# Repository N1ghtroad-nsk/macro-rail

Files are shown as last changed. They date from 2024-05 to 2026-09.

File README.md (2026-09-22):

# Macro Slider | Слайдер для макросъемки

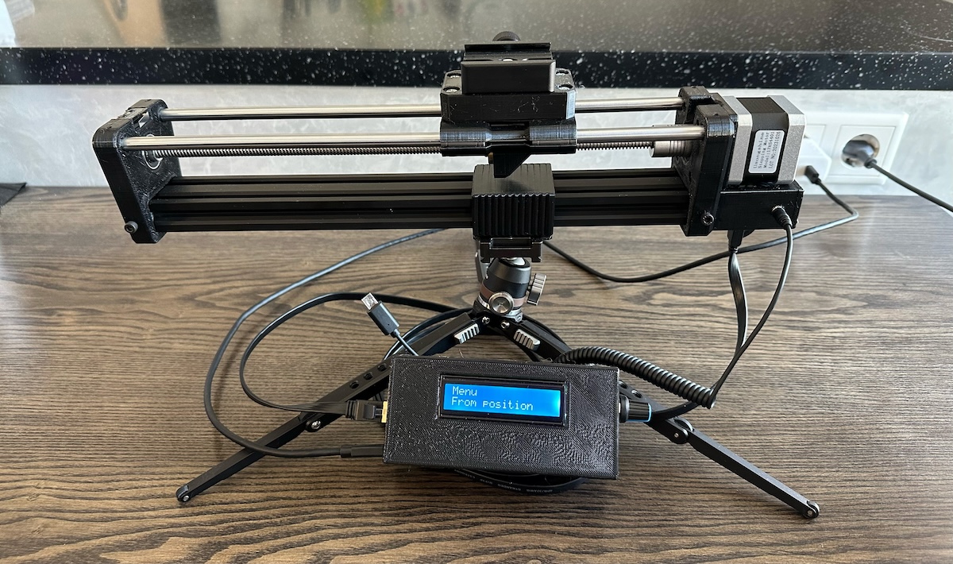
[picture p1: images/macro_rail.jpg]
Macro Rail


- [Macro Slider | Слайдер для макросъемки](#macro-slider--слайдер-для-макросъемки)
- [RU](#ru)
  - [Структура](#структура)
  - [Компоненты](#компоненты)
    - [Пульт](#пульт)
    - [Рельса](#рельса)
    - [Крепление](#крепление)
  - [Схема](#схема)
  - [Arduino](#arduino)
    - [Зависимости](#зависимости)
    - [Настройка](#настройка)
- [EN](#en)
  - [File Structure](#file-structure)
  - [Bill Of Materials (BOM)](#bill-of-materials-bom)
    - [Remote](#remote)
    - [Rail](#rail)
    - [Mounting](#mounting)
  - [Schematic](#schematic)
  - [Arduino](#arduino-1)
    - [Dependencies](#dependencies)
    - [Settings](#settings)

# RU

## Структура

arduino/macro_rail - [скетч для Arduino](/Arduino/macro_rail/)  
stl - [детали для 3D-печати](/STL/)  
pcb - [схема и плата](/PCB/)  

## Компоненты 

### Пульт

- [Печатная плата](/PCB/macro_rail_pcb.pdf) - 1шт
- Arduino nano (LGT8F328P-LQFP32) - 1шт
- Шаговый мотор Nema17 (17HS4401) - 1шт
- Драйвер шагового двигателя TMC2209 - 1шт
- Энкодер с кнопкой EC11 - 1шт
- Экран LCD1602C с i2c-интерфейсом - 1шт
- Оптопара транзисторная PC817 - 1шт
- Концевик SS-5GL - 1шт
- Понижающий преобразователь с 12В до 5В - 1шт
- Type-C QC 12В - 1шт
- XH2.54-4P male порт, female кабель - 1шт
- XH2.54-5P male порт, female кабель - 1шт
- XH2.54-8P male порт, female кабель - 1шт
- PH2.0-6P female кабель -1шт
- RJ45 порт - 2шт
- Audio female 2.5mm Jack PJ201M - 1шт

### Рельса

- Вал направляющий 8 мм длина 300мм - 1шт
- Линейный подшипник LM8UU с внутренним диаметром 8 мм - 4шт
- Трапецеидальный винт Т8 (Tr8x2) (Длина винта 300 мм, Шаг винта 2 мм. Однозаходный) - 1шт
- Латунная гайка для винта Tr.8x2 (Однозаходная) - 1шт
- Подшипник KP08 опорный фланцевый (8мм) - 1шт
- Муфта эластичная с отверстиями 5мм/8мм и резьбовым зажимом (CR 5x8 мм) - 1шт
- Профиль конструкционный V20х40SH 20x40 мм, паз 6 мм длина 300 мм - 1шт
- Заглушка торцевая 20x40 для профиля 2040 - 1шт
- Заглушка пазовая под паз 6 мм для профиля 2040 - 1шт
- Сухарь пазовый М4, паз 6 - 5шт
- Болт 1/4 длина 3/4 (для крепления площадки) - 1шт
- Arca Swiss Quick Release Plate - 1шт
- 2.5mm Remote Shutter Release Cable - 1шт
- Ethernet кабель (тестировался кабель до 2м) - 1шт

### Крепление

- M3 болт 6мм - 10шт
- M3 болт 10мм - 16шт
- М3 болт 16мм - 2шт
- M4 болт 14мм - 5шт
- M4 болт 30мм - 4шт
- М3 гайка - 2шт
- М4 гайка - 9шт
- М4 шайба - 8шт
- M6 шайба - 1шт

## Схема

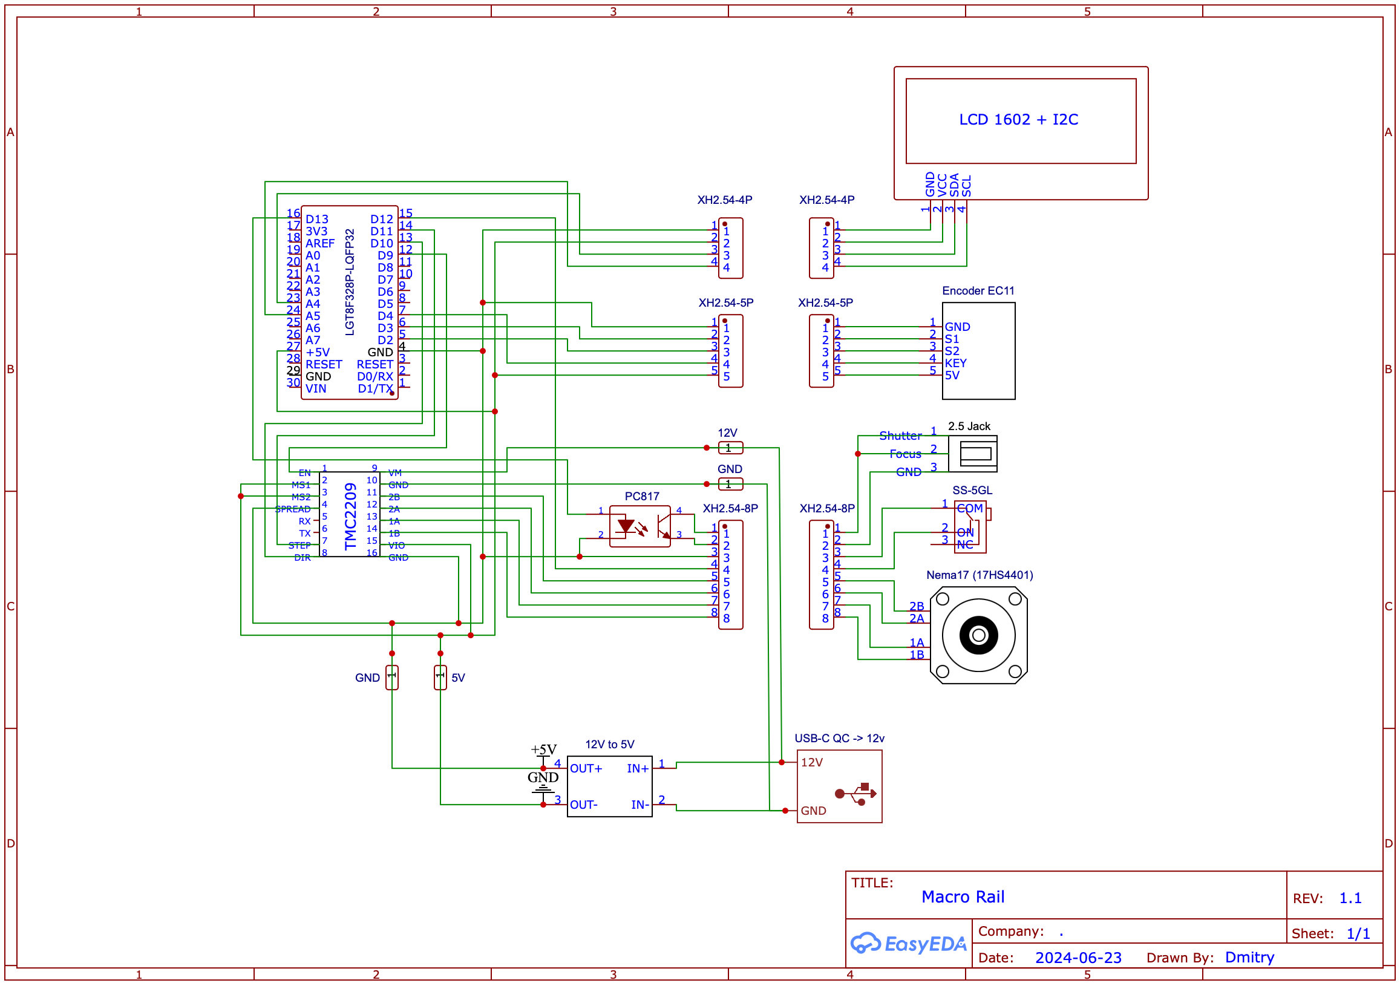
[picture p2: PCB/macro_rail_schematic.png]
Macro Rail Schematic


## Arduino

### Зависимости

Чтобы скетч собрался сначала нужно установить библиотеки в Arduino IDE

В Arduino IDE в Library Manager нужно установить:  

- ArduinoSTL
- EncButton
- LiquidCrystal I2C
- TimeOne

### Настройка

Трапецеидальный винт Т8 может быть с любым шагом, но его шаг должен быть изменен в скетче  

файл Globals.cpp  
StepperT<STEPP_ENA, STEPP_STEP, STEPP_DIR, STEPP_END, 16, 200, **8**> g_stepper;  

файл Globals.h  
extern StepperT<STEPP_ENA, STEPP_STEP, STEPP_DIR, STEPP_END, 16, 200, **8**> g_stepper;  

# EN

## File Structure

arduino/macro_rail - [arduino sketch](/Arduino/macro_rail)  
stl - [3D-printable parts](/STL/)  
pcb - [schematic and PCB layout](/PCB/)  

## Bill Of Materials (BOM)

### Remote

- PCB - 1 pc
- Arduino nano (LGT8F328P-LQFP32) - 1 pcs
- Nema17 Stepper Motor (17HS4401) - 1 pcs
- TMC2209 Stepper Driver - 1 pcs
- EC11 Encoder with Button - 1 pcs
- LCD1602C Screen with i2c interface - 1 pcs
- PC817 Transistor Optocoupler - 1 pcs
- SS-5GL Limit Switch - 1 pcs
- 12V to 5V Step-Down Converter - 1 pcs
- Type-C QC 12V - 1 pcs
- XH2.54-4P male port, female cable - 1 pcs
- XH2.54-5P male port, female cable - 1 pcs
- XH2.54-8P male port, female cable - 1 pcs
- PH2.0-6P Female cable - 1 pcs
- RJ45 port - 2 pcs
- 2.5mm Audio Female Jack PJ201M - 1 pcs

### Rail

- 8mm Guide Rod, 300mm length - 1 pcs
- LM8UU Linear Bearing with 8mm inner diameter - 4 pcs
- Trapezoidal Screw T8 (Tr8x2) (Screw length 300mm, thread pitch 2mm, single-start) - 1 pcs
- Brass Nut for Tr8x2 Screw (single-start) - 1 pcs
- KP08 Flanged Bearing (8mm) - 1 pcs
- Elastic Coupling with 5mm/8mm holes and threaded clamp (CR 5x8mm) - 1 pcs
- V20x40SH Construction Profile, 20x40mm, 6mm slot, 300mm length - 1pcs
- End Cap for 20x40 profile - 1 pcs
- Slot Cap for 6mm slot profile 2040 - 1 pcs
- M4 Slot Nut, 6mm slot - 5 pcs
- 1/4” Bolt, 3/4” length (for platform mounting) - 1 pcs
- Arca Swiss Quick Release Plate - 1 pcs 
- 2.5mm Remote Shutter Release Cable - 1 pcs
- Ethernet Cable (tested with cable up to 2m) - 1 pcs

### Mounting

- M3 Screw 6mm - 10 pcs
- M3 Screw 10mm - 16 pcs
- M3 Screw 16mm - 2 pcs
- M4 Screw 14mm - 5 pcs
- M4 Screw 30mm - 4 pcs
- M3 Nuts - 2 pcs
- M4 Nuts - 9 pcs
- M4 Washers - 8 pcs
- M6 Washer - 1 pcs

## Schematic

Macro Rail Schematic

## Arduino

### Dependencies

To compile the sketch, first install the necessary libraries in the Arduino IDE.  

In Arduino IDE, install the following through the Library Manager:  

- ArduinoSTL
- EncButton
- LiquidCrystal I2C
- TimeOne

### Settings

You can use a T8 trapezoidal screw with any thread pitch, but you will need to adjust the setting in the sketch..  

In the Globals.cpp file:  

StepperT<STEPP_ENA, STEPP_STEP, STEPP_DIR, STEPP_END, 16, 200, **8**> g_stepper;  

In the Globals.h file:  

extern StepperT<STEPP_ENA, STEPP_STEP, STEPP_DIR, STEPP_END, 16, 200, **8**> g_stepper;

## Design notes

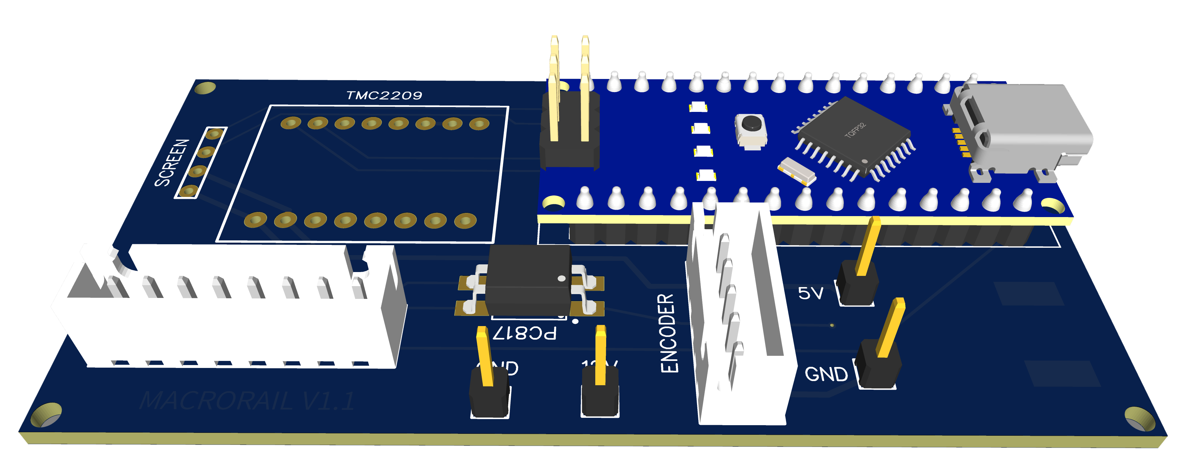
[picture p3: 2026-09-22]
images/pcb_3d.png

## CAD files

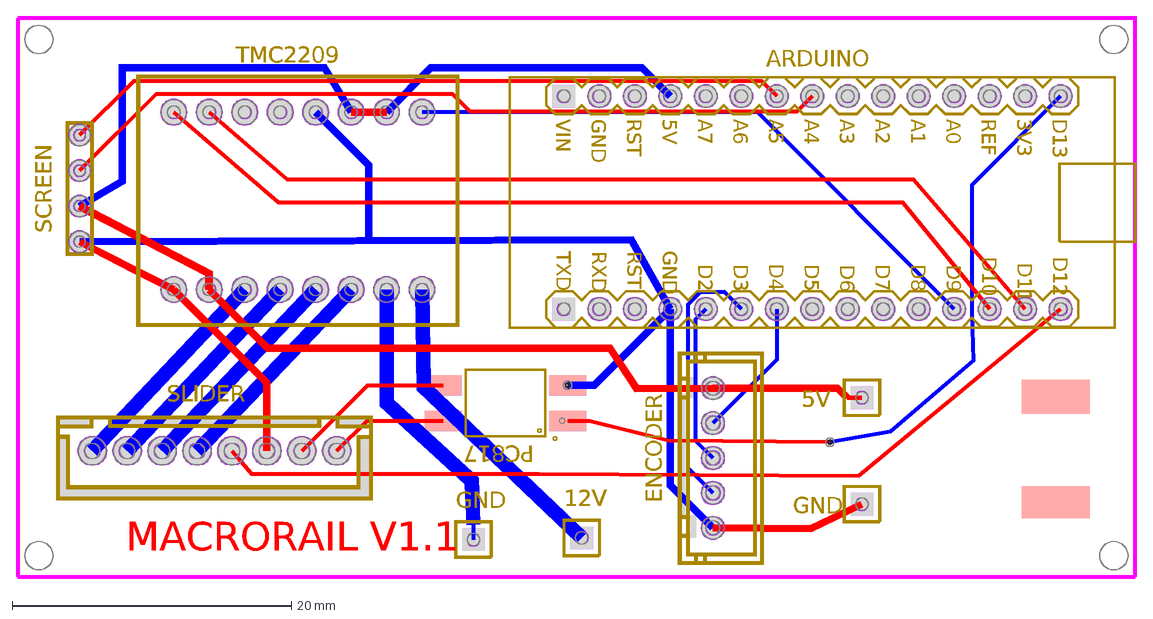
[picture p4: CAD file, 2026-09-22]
PCB/macro_rail_pcb.dxf
MACRORAIL V1.1
5V
GND
12V
SCREEN
SLIDER
ARDUINO
D13
3V3
REF
A0
A1
A2
A3
A4
A5
A6
A7
RST
VIN
D12
D11
D10
D9
D8
D7
D6
D5
D4
D3
D2
RXD
TXD
TMC2209
ENCODER
PC817

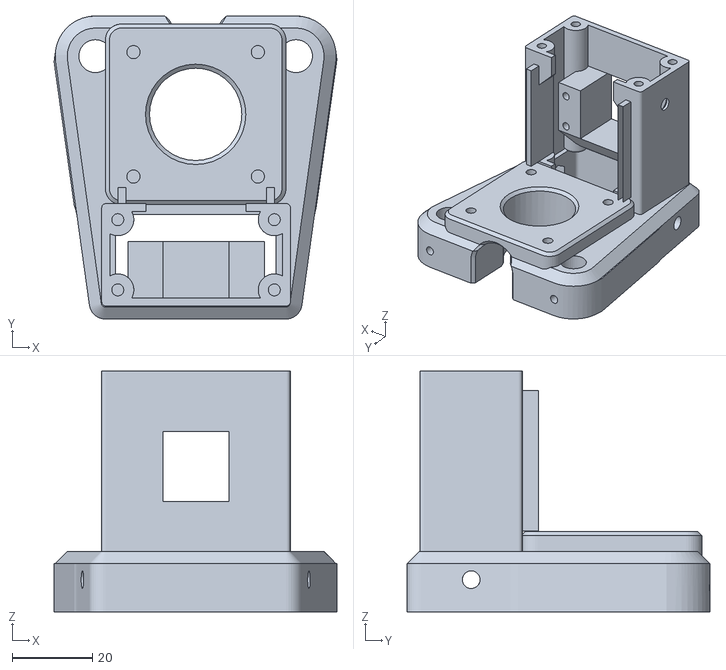
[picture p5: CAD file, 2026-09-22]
STL/rail/frame_back.stl
70.5 x 75.5 x 59.9

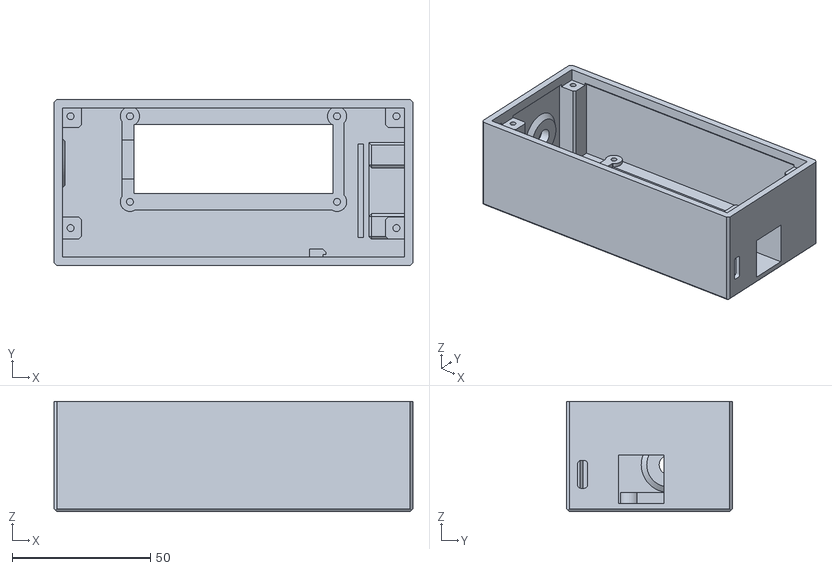
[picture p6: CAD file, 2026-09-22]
STL/remote/controlcase_body.stl
130.0 x 60.0 x 40.0

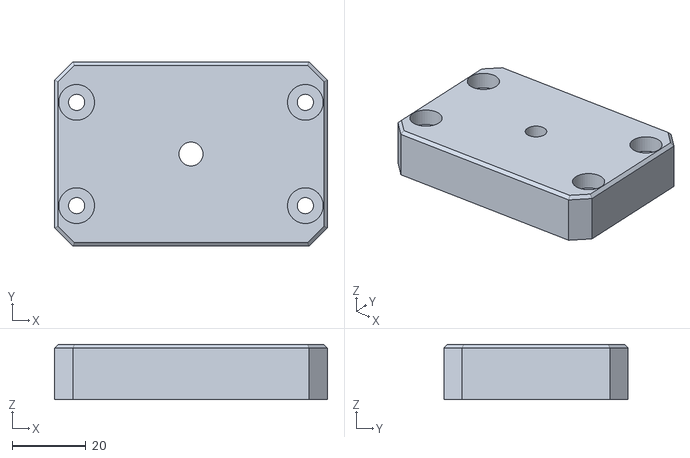
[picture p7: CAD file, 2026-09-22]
STL/rail/carriage_top.stl
74.0 x 50.0 x 15.0

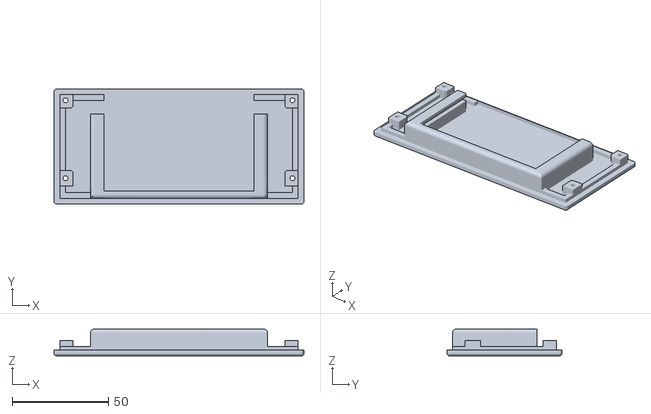
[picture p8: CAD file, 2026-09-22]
STL/remote/controlcase_lid.stl
130.0 x 60.0 x 14.0

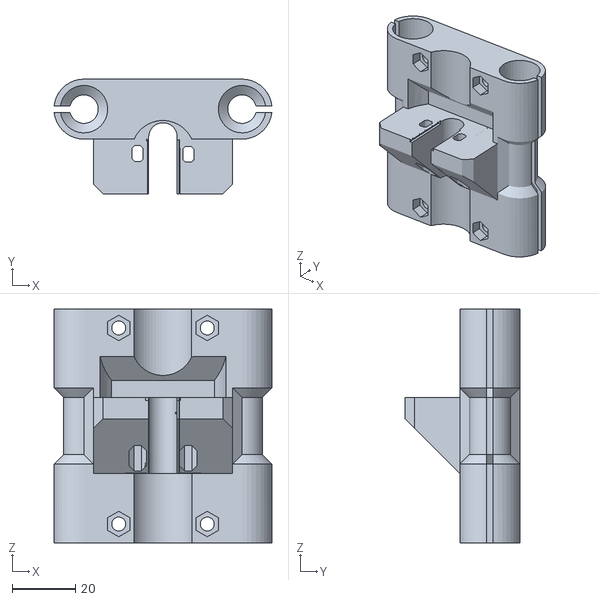
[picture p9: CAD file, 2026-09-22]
STL/rail/carriage_body.stl
68.9 x 36.3 x 74.0

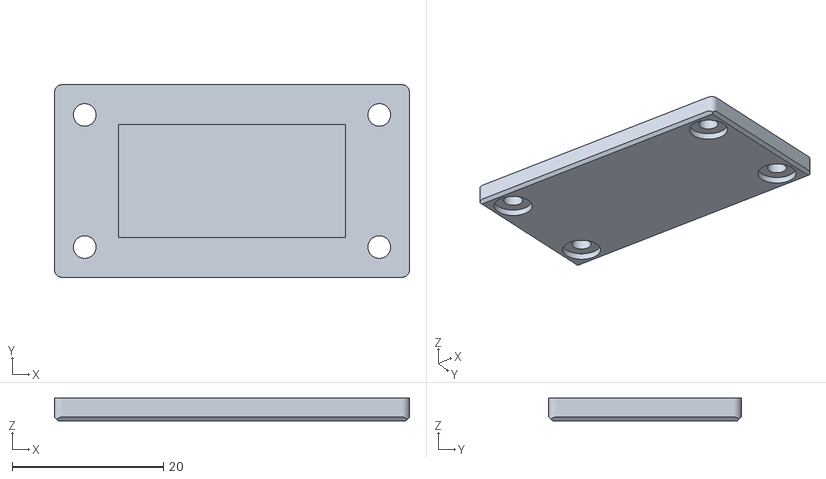
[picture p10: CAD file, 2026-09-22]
STL/rail/frame_back_lid.stl
47.0 x 25.5 x 3.00

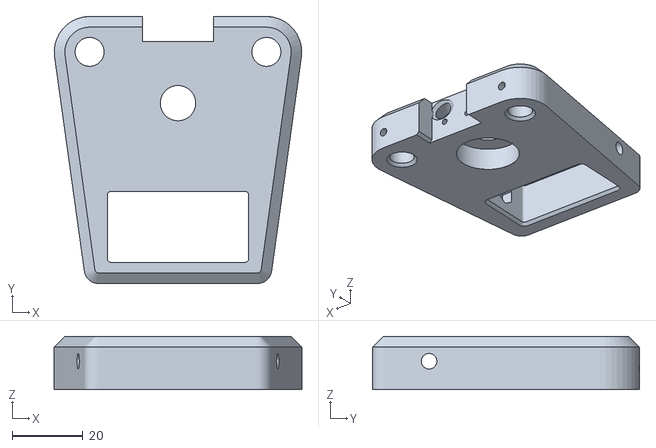
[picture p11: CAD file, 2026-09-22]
STL/rail/frame_front.stl
70.0 x 75.5 x 15.0

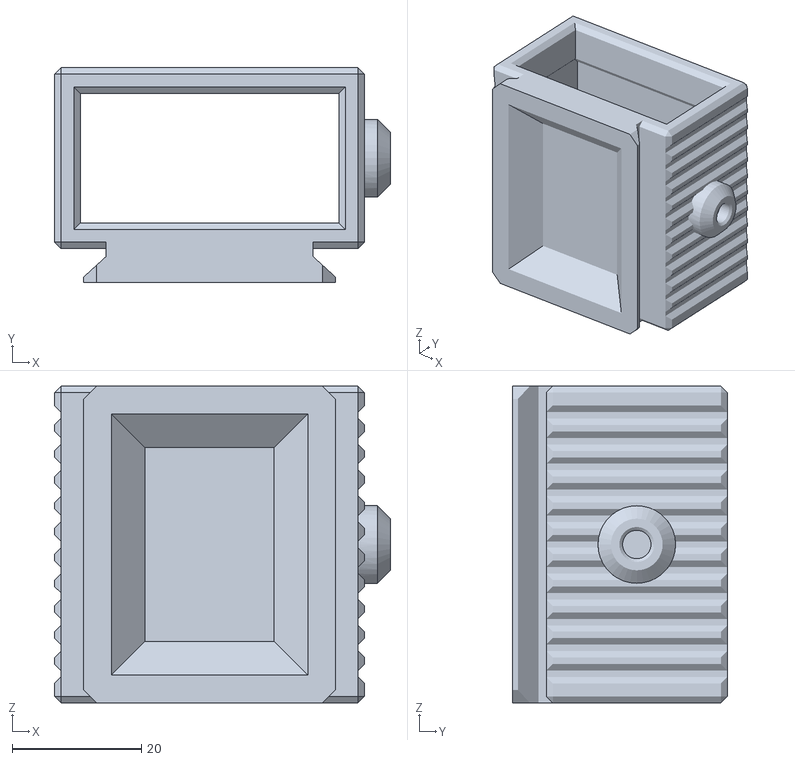
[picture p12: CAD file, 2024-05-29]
STL/rail/frame_tripod_adapter.stl
52.0 x 33.2 x 49.0

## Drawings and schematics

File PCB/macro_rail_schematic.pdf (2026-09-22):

## LCD 1602 + I2C

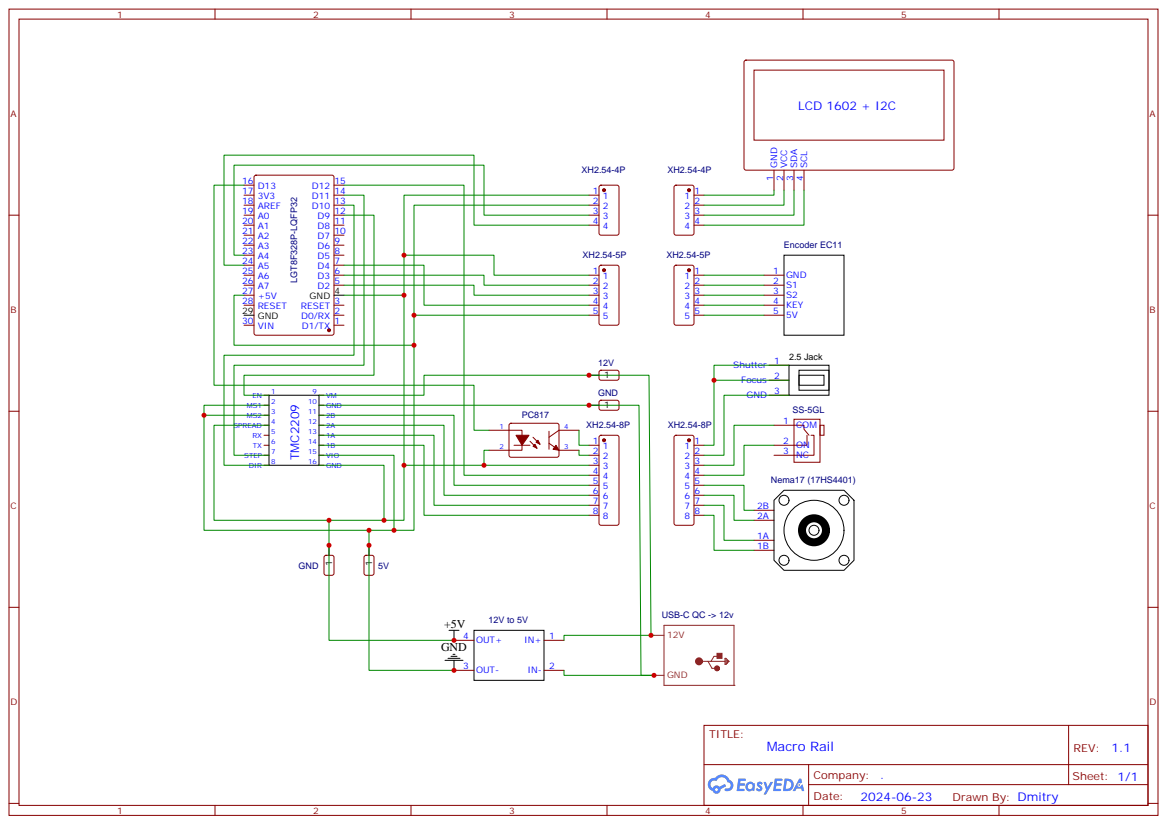
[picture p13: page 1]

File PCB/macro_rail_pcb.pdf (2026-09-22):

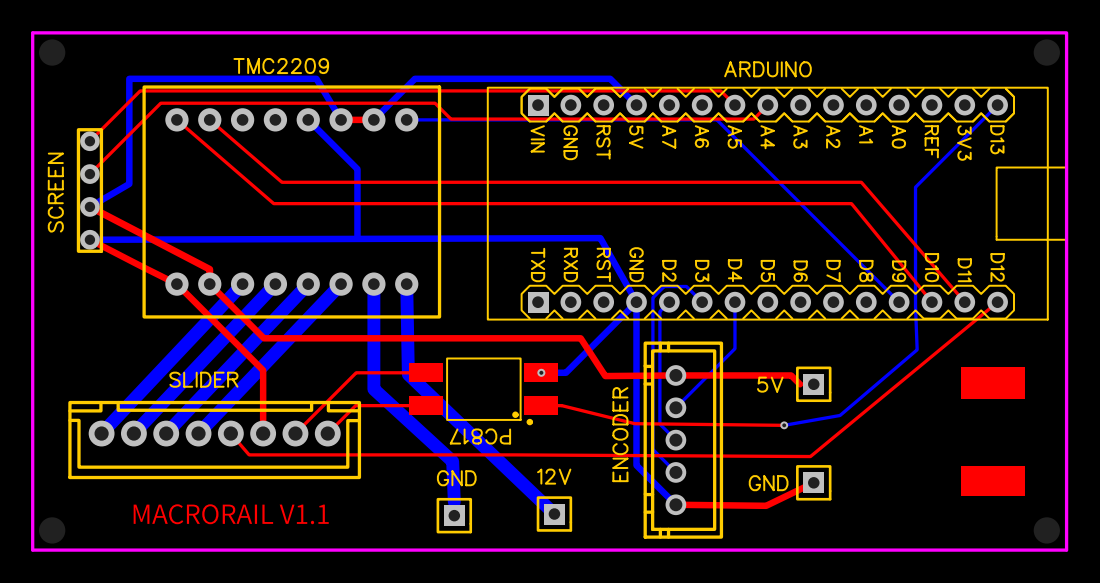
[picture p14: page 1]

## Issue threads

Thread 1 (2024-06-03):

TimerOne.h

ddyugaev, 2024-06-03:
Отсутствует файл TimerOne.h

```
macro_rail.ino:1:10: fatal error: TimerOne.h: No such file or directory
 #include <TimerOne.h>
          ^~~~~~~~~~~~
compilation terminated.
exit status 1
```

ddyugaev, 2024-06-03:
Извиняюсь, нужно было установить через library manager

Closed 2024-08-22.

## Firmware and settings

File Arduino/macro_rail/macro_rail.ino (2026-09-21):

#include <TimerOne.h>
#include <ArduinoSTL.h>

#include "Globals.h"

#include "MenuMode.h"
#include "MainMenu.h"
#include "FastManualMode.h"
#include "FromPositionMode.h"
#include "ToPositionMode.h"
#include "PhotoMode.h"
#include "SaveMode.h"
#include "ValueMode.h"
#include "BoolMode.h"
#include "FreeMode.h"

MainMenu g_mainMenu;

void timerInterrupt() {
  g_stepper.update();
}

void setup() {
  g_lcd.init();
  g_lcd.backlight();
  g_display.init();
  g_stepper.init();

  g_encoder.setEncType(EB_STEP2);

  g_settings.photoSettings.loadFromEEPROM(g_photoSettingsAddress);

  g_camera.setup();

  MenuMode * settingsMenu = new MenuMode(F("Settings"));

  g_mainMenu.insertMode(new FromPositionMode());
  g_mainMenu.insertMode(new ToPositionMode());
  g_mainMenu.insertMode(new PhotoMode());

  g_mainMenu.insertMode(new FreeMode());

  settingsMenu->insertMode(new ValueMode<float>(F("Frame depth"), F("mm"), g_settings.photoSettings.frameDepth, 0.01));
  settingsMenu->insertMode(new ValueMode<unsigned int>(F("Calm time"), F("mSec"), g_settings.photoSettings.calmMsec, 10));
  settingsMenu->insertMode(new ValueMode<unsigned int>(F("Exposure time"), F("mSec"), g_settings.photoSettings.exposureMsec, 10));
  settingsMenu->insertMode(new ValueMode<unsigned int>(F("Camera delays"), F("mSec"), g_settings.photoSettings.cameraShotDelay, 10));
  settingsMenu->insertMode(new BoolMode(F("Mirror PreUp"), g_settings.photoSettings.useMirrorPreUp));

  settingsMenu->insertMode(new SaveMode());

  settingsMenu->finalize();
  g_mainMenu.insertMode(settingsMenu);
  
  g_mainMenu.init();

  Timer1.initialize(1000);
  Timer1.attachInterrupt(timerInterrupt);
}

void loop() {
  g_encoder.tick();
  g_mainMenu.update();
  g_camera.update();
}

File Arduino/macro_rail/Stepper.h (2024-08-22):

#pragma once

#include <Arduino.h>
#include <TimerOne.h>

#define DERATTLING_DELAY 10

class Stepper {
public:
  virtual void init() = 0;    
  virtual void enable() = 0;
  virtual void disable() = 0;
  virtual void setSpeed(int rpm) = 0;
  virtual void rotateSteps(long steps) = 0;
  virtual void startRotate(int direction) = 0;
  virtual void rotateDistance(float mm) = 0;  
  virtual void stop() = 0;
  virtual void update() = 0;
  virtual long stepsLeft() = 0;
  virtual bool endstopHit() = 0;

  virtual void resetPosition() = 0;
  virtual long getPosition() = 0;

  virtual double stepsToMm(long steps) = 0;
  virtual long mmToSteps(double mm) = 0;

  virtual void goToPosition(long position) = 0;
};

template <byte ENA, byte STEP, byte DIR, byte ENDSTOP, byte INTERP, int STEPSPERROT, int DISTPERROT>
class StepperT : public Stepper {
public:
  StepperT() {
  }

  void init() {
    pinMode(ENA, OUTPUT);
    pinMode(STEP, OUTPUT);
    pinMode(DIR, OUTPUT);
    pinMode(ENDSTOP, INPUT_PULLUP);
    disable();
  }
    
  void enable() {
    stop();
    digitalWrite(ENA, LOW);
  }

  void disable() {
    stop();
    resetPosition();
    digitalWrite(ENA, HIGH);
  }

  void setSpeed(int rpm) {
    Timer1.setPeriod(60000000 / rpm / STEPSPERROT / INTERP);
  }

  void rotateSteps(long steps) {
    m_steps += steps;
    m_infinite = false;
  }

  void startRotate(int direction) {
    if (m_steps * direction < 0)
      m_steps = 0;
    else
      m_steps = direction;
    m_infinite = true;
  }

  void rotateDistance(float mm) {
    if (m_steps == 0)
      m_steps = mmToSteps(mm);
    m_infinite = false;
  }

  void stop() {
    m_steps = 0;
    m_infinite = false;
  }

  void update() {
    if (m_steps == 0)
      return;
    if (endstop() && m_steps > 0) {
      m_endstopped = true;
      stop();
    }
    if (m_steps != 0) {
      m_endstopped = false;
      digitalWrite(DIR, m_steps > 0 ? HIGH : LOW);
      digitalWrite(STEP, m_stepPin ? HIGH : LOW);
      m_stepPin = !m_stepPin;
      m_position += m_steps > 0 ? 1 : -1;
      if (!m_infinite)
        m_steps += m_steps > 0 ? -1 : 1;
    }
  }

  long stepsLeft() {
    return m_steps;
  };

  bool endstop() {
    const bool hit = digitalRead(ENDSTOP) == LOW;
    if (!hit)
      m_derattlingTime = millis();
    else if (millis() - m_derattlingTime > DERATTLING_DELAY || m_derattlingTime > millis())
      return true;
    return false;     
  }

  bool endstopHit() override {
    return m_endstopped;
  }

  virtual void resetPosition() {
    m_position = 0;
  };

  virtual long getPosition() {
    return m_position;
  };

  virtual double stepsToMm(long steps) {
    return double(steps) * DISTPERROT / STEPSPERROT / INTERP;
  }
  virtual long mmToSteps(double mm) {
    return mm/DISTPERROT*STEPSPERROT*INTERP;
  }

  virtual void goToPosition(long position) {
    stop();
    rotateSteps(position - m_position);
  }

private:
  long m_steps;
  long m_position;
  bool m_stepPin;
  bool m_infinite;
  bool m_endstopped;
  long m_derattlingTime = 0;
};

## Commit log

2024-08-22 Fixed display flickering on endstop hit
    [FastManualMode.cpp]
2024-08-22 Added deratling to endstop
